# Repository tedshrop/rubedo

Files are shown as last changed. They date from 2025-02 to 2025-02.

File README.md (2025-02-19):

# Rubedo - Tedshrop Fork
## A tool for automatically calibrating pressure advance at runtime.
This tool is an elaboration on the work done by furrysalamander. The original version can be found [here](https://github.com/furrysalamander/rubedo).

Most of the code is still original, most of the rest of this readme is still original. I will be updating it as I expand the functionality and then rewrite this whole section.

I've modified the code to expose additional variables that can be set both in the constants.py file, and at runtime through gcode macro arguments.

I've also modified the setup to use the existing 3do nozzle cam, and mount the laser behind the stealthburner out of the way (unless you have a blobifier).

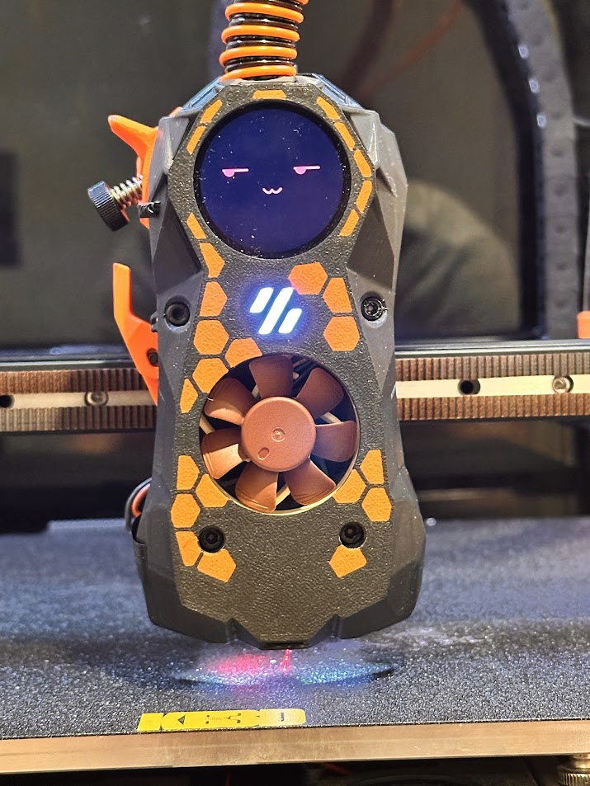
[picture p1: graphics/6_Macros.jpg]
Printer with the system installed


*The system installed on my printer*

Calibration pattern compared with the control and results

*On the left is the pattern that was scanned. The middle pattern shows the pattern printed with pressure advance disabled, and the pattern on the right shows a pattern printed with the calibrated value.*

***
### Disclaimer
This tool is still very much experimental. I hope that someday it will grow to be more robust and user friendly, but right now you should know at least a little bit of Python if you're interested in trying it out. It's not perfect. The gcode that is generated may not play nicely with your printer. I would recommend keeping the emergency stop button within close reach the first time you run the calibration, just to be safe.
***

## Things you will need to setup on your printer:
* A Stealthburner (for now). It could be adapted to any system that has a nozzle camera.
* A high quality USB camera. I use the 4K 3DO nozzle camera in the default Stealthburner location.
* An adjustable focus line laser. I tested a fixed focus laser earlier on, but the beam was super thick and there was no way to adjust it. I have a laser like [this](https://www.amazon.ca/gp/product/B07L428BDG/ref=ppx_yo_dt_b_search_asin_image?ie=UTF8&th=1). 
* The laser mounted on the toolhead. I am using the mount `Laser Mount V4.stl` located in the `camera_mounts` directory. Please note: My setup is for the UHF variant of the Stealthburner, and I haven't made a mount for the regular sized SB yet. If you modify it or make one for your application, please let me know if I can post it back here for others. If you're using the Blobifier, you'll need to reprint your shaker. You can find one that will clear the laser in `camera_mounts`.

***
## HARDWARE INSTALLATION

Here's the process to get the laser installed:

* Step 0 - Print the mount
* Step 1 - Flip it up on it's face and heat your bed 
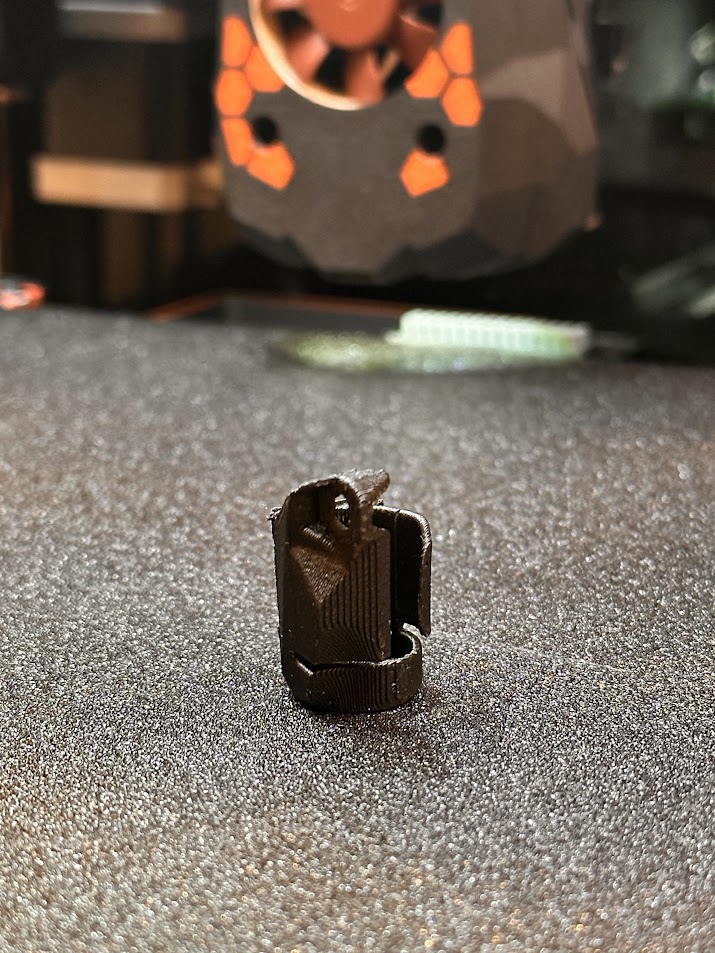
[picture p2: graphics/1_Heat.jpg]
Laser mount oriented lens-side down on print bed
 

* Step 2 - When the print is hot, insert the laser module with the lens oriented as shown below
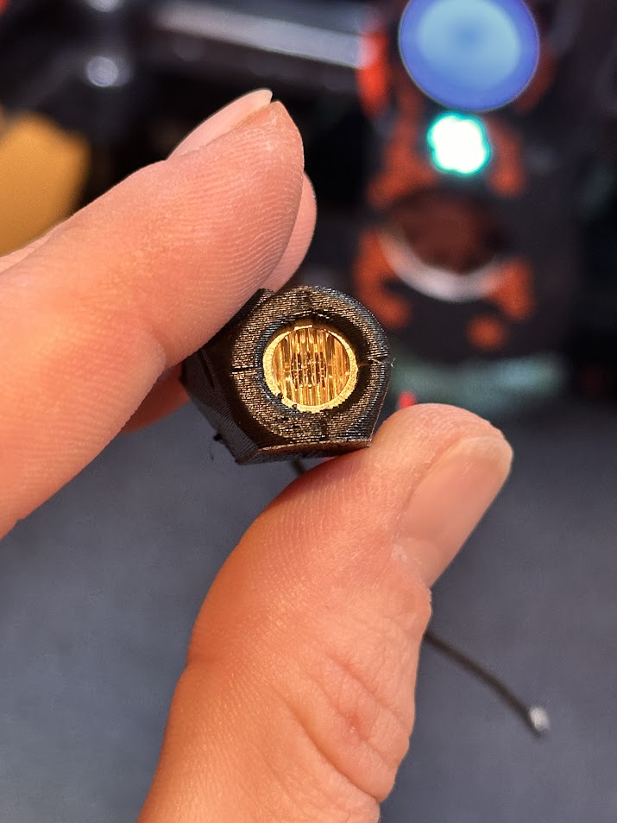
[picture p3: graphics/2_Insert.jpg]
Laser module inside of print
 

* Step 3 - Remove the cylindrical cover of the laser module, then replace and resolder the wires (they're dinky) and install it on the back of the Stealthburner.
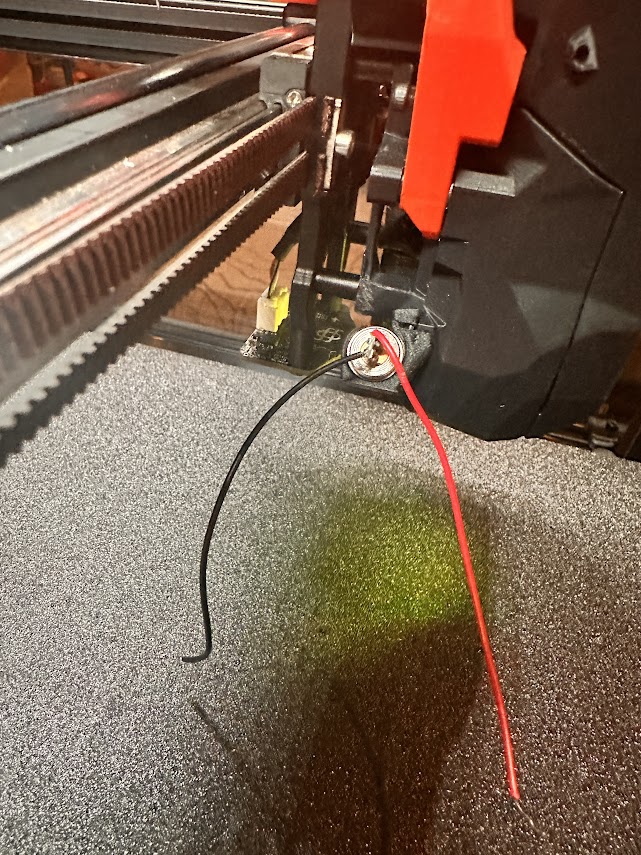
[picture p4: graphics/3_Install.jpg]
Module installed with loose wires
 

* Step 4 - Focus your laser:  Turn your printer on, move it to ~8mm from the bed and look through your nozzle camera. Power the laser with a 2.5-5V source (coin cell batter works well). Rotate the laser within the lens body in order to focus it perfectly to the bed.
* Step 5 - Route your wires to any 5v fan output. It's possible to use a 12v or 24v output if you put the appropriate resistor in series. If you're not familiar with that, do a google search for LED resistor calculator.
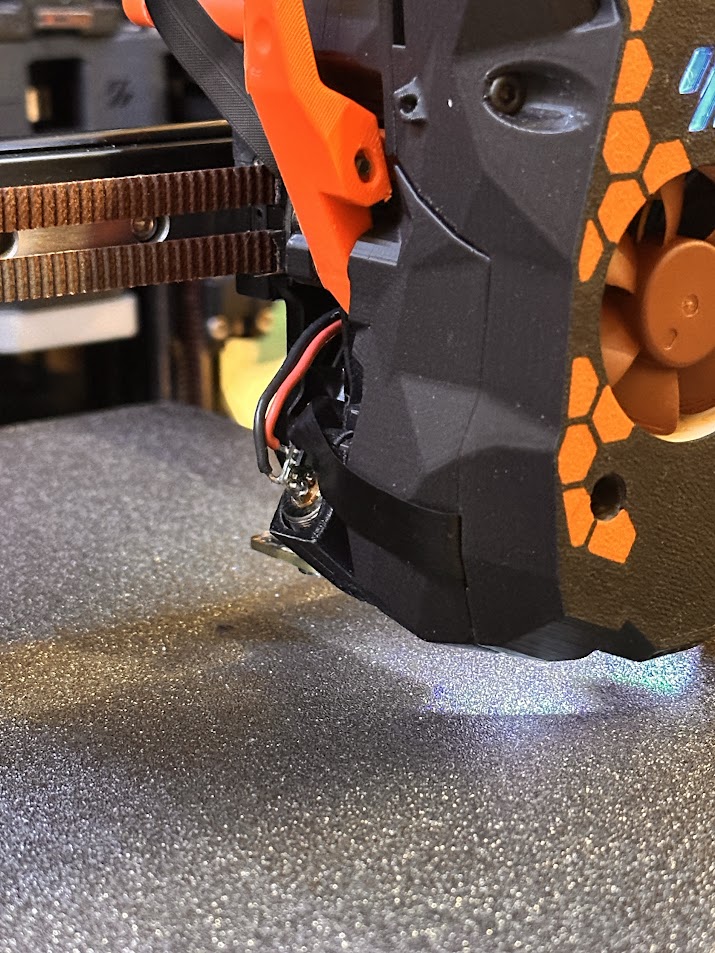
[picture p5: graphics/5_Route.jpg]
Module installed with wires tightly entering Stealthburner
 

## SOFTWARE INSTALLATION

* Install a few  dependencies:
    ```
    sudo apt install ffmpeg python3-opencv python3-matplotlib python3-aiohttp python3-websocket
    cd ~
    git clone https://github.com/tedshrop/rubedo.git
    ```
* copy rubedo_macros.cfg to your printer configuration folder and put the following at the top of your printer.cfg. Go through and set the PIN# for the laser as you have it installed on your machine.
    ```
    [include rubedo_macros.cfg]
    ```
* Do a firmware restart. You should now be able to test your laser by using the LASER_ON and LASER_OFF macros.
* Turn your laser on and open the camera image on mainsail/fluidd. Slide a piece of first-laser filament into view (like a purge line or brim) roughly 3mm in front of the nozzle, or wherever it's perfectly in focus. On your browser, right click the camera image and save it. Open in microsoft paint or any other image editing software to determine what the crop should be. In my image for example, the crop was 250px by 250px, starting from 1500,1500.
View of the laser on filament 

* Go through the `constants.py` file, and adjust whatever you need to in order to set the defaults the way you like. This can always be changed later at runtime.

## Running the Script

* Standalone: The script can be started by using the gcode macro RUBEDO.
* As part of your startup script (in your slicer, don't put in your PRINT_START macro) by adding "RUBEDO STANDALONE=False"
* You can call a set a bunch of variables by using gcode arguments. The options are as follows:

### BED_TEMP
### EXTRUDER_TEMP
### TOOL
### FINISHED_X 
Park location
### FINISHED_Y 
Park location
### NOZZLE_DIAMETER
### SPEED
### FLOW 
### ACCELERATION
### HOP
### LAYER_HEIGHT
### RETRACTION_DISTANCE

You can save the variables that you call as the new default if you add SAVE=1 to the arguments.

***

# Code Organization
The code that allows for hands free calibration is in `main.py`. Once you've configured everything correctly, you should be able to run the script and get recommended pressure advance value.  If you have `VALIDATE_RESULTS` enabled, the printer will print another two patterns, one w/ PA disabled, and another with the selected value. Most users probably won't want this, so feel free to turn it off.  It also makes it hard to find the recommended value in the scripts output.

If you want to test a different range of pressure advance values, or change where the calibration pattern is printed, you can do so by editing the parameters used for the PatternInfo object created at the start of the main function. By default, the pattern is printed at (30, 30), and tests 10 PA values between 0 and 0.06.

### `pa.py`
This file contains code for generating the calibration pattern gcode.

### `record.py`
This file contains functions for recording video clips of the printed lines.

### `processing.py`
This file contains a few utilities that filter and transform the video frames to help minimize noise.

### `analysis.py`
This file contains the code that generates height maps for each line, and then computes the line deviation for each heightmap.

### `visualization.py`
This file contains several utilities for visualizing the height maps and data that is generated from the scans. Currently, some of the functions here are in disrepair, as I needed the output during early development, but haven't used them since.

### `generate_bulk_scans.py`
This file will print 27 copies of the calibration pattern, scan all of them, and then save the results for later analysis. I used this while working on my research paper for this project to measure how consistent the system was.

### `generate_report_data.py`
This script consumes the files generated by the `generate_bulk_scans.py` script, and generates height map visualizations for each line that was scanned. In addition, it generates charts that aggregate the data from all scans to visualize the overal consistency of the calibration process.

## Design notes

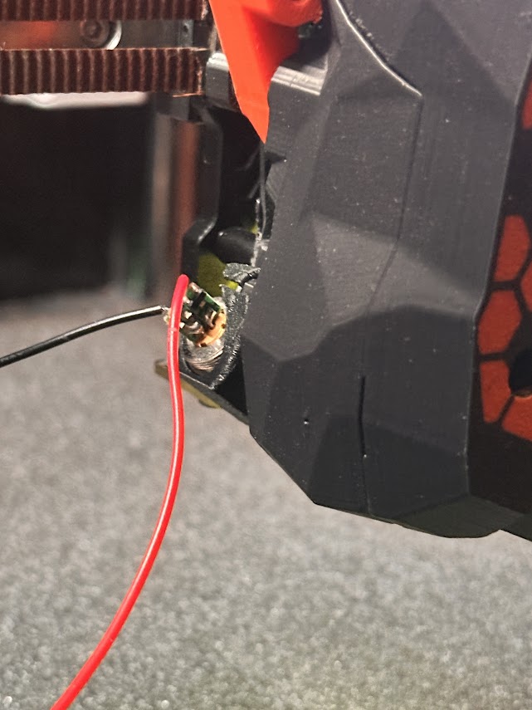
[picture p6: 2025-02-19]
graphics/4_Route.jpg

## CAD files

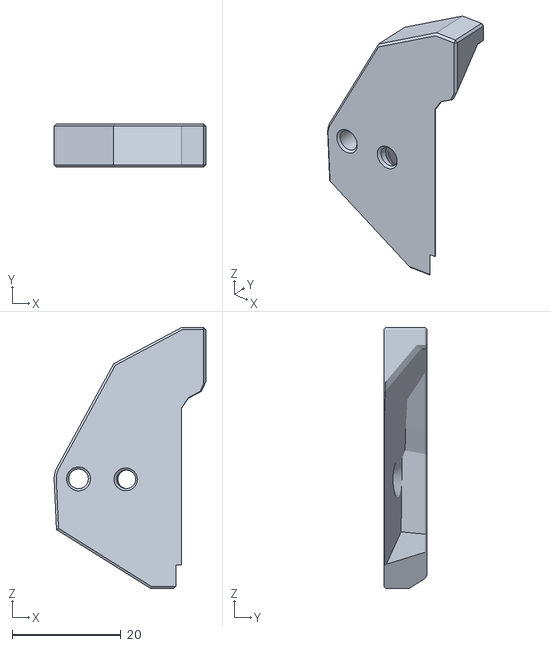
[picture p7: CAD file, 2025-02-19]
camera_mounts/Modified Blobifier Shaker.stl
28.0 x 8.00 x 48.1

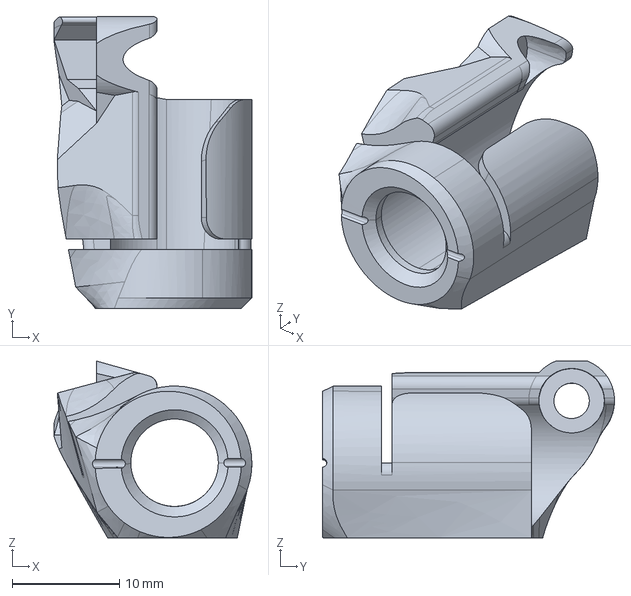
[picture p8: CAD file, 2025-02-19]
camera_mounts/Laser Mount V4.stp
18.5 x 27.3 x 16.5 mm

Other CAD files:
camera_mounts/Laser Mount V4.stl

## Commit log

2025-02-16 Update constants.py
    Updated for my camera crop. Probably close to most users of 3do nozzle cam in default position.
2025-02-16 Corrected Video Device Name
2025-02-19 Updated Readme and Images
    [3DO_Mount_v2.step, Laser Mount V4.stl, Laser Mount V4.stp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]
